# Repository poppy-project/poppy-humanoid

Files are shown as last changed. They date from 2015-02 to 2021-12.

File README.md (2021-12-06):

Poppy Humanoid
===================


Poppy Humanoid is an open-source and 3D printed humanoid robot. Optimized for research and education purposes, its modularity allows for a wide range of applications and experimentations.

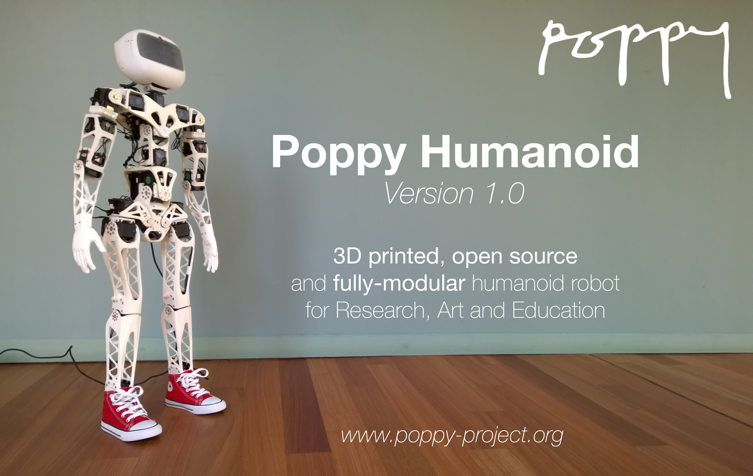
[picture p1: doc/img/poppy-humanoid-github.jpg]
Trunk Assembled


### Open Source

All the technological development work made in the Poppy project is freely available under open source licenses. Only the name usage *"Poppy"* is restricted and protected as an international trademark, please contact us if you want to use it or have more information.

| License | Hardware | Software |
| --- | :---: | :---: |
| Title  | [Creatives Commons BY-SA](http://creativecommons.org/licenses/by-sa/4.0/)  |[GPL v3](http://www.gnu.org/licenses/gpl.html)  |
| Logo  |   |GPL V3 (http://www.gnu.org/licenses/gpl.html)  |

**Please keep references to the [Poppy project (www.poppy-project.org)](https://www.poppy-project.org/) and [authors](doc/authors.md) when you use or fork this work.**

### Looking for the Solidworks files ?

We are using a GitHub feature called GIT LFS. It is great for versionning solidworks files but it stills lack basic features. If you download directly solidworks files from this web page, you will get an empty file...

You have two option:

1. Download the last official Solidworks version in the [release](https://github.com/poppy-project/poppy-humanoid/releases). You will also find STL, STEP and parasolid files.
- Clone locally this repository following [this guide](doc/en/cloning.md). This solution is only for people desiring to contribute or develop news hardware features for Poppy.

## Build your own Poppy Humanoid

Building a complete Poppy Humanoid costs $8000-9000 with about 60% for buying the 25 Robotis Dynamixel actuators required. The full BOM is available here >> [Bill Of Material](https://docs.poppy-project.org/en/assembly-guides/poppy-humanoid/bom.html).

**The STL files are available in [the releases](https://github.com/poppy-project/poppy-humanoid/releases) of this repository.**

Then the process to assemble a complete Poppy Humanoid takes about 7hrs for  handyman people.

**For more informations, refer to the [assembly instructions](https://docs.poppy-project.org/en/assembly-guides/poppy-humanoid/)**.

### Install poppy-humanoid
#### Install a Poppy board
Poppy Humanoid is made to work with a Raspberry Pi 3 or 4. We provide our own [system image](https://github.com/poppy-project/poppy-humanoid/releases) that can be directly copied to the SD-card or MMC. You can refer to the [documentation](http://docs.poppy-project.org/en/installation/burn-an-image-file.html) for more details. Note that if you buy it as a kit from one of the reseller you will also get a pre-installed SD-card.

### Install the software tools locally

You way also connect Poppy Huanoid's motors directly on your own computer with a USB2Dynamixel or USB2AX adapter instead of using the embedded Raspberry Pi 3/4 board. Just install software with pip: `pip install poppy-humanoid`.

**For more informations, refer to the [poppy documentation](http://docs.poppy-project.org/en/installation/index.html)**.

## Support
You need support ?
The [Poppy forum](https://forum.poppy-project.org) is the best (and single) place to ask for help.

You can in particular check for the [Poppy Humanoid category](https://forum.poppy-project.org/c/poppy-creatures/humanoid).

## Contribution

If you are interrested by contribuing to the Poppy project, you can **take a look at [open issues](https://github.com/poppy-project/poppy-humanoid/issues) and [call for contributions](https://forum.poppy-project.org/tags/call-for-contributions)**.

Morevover, the Poppy project involves a very large scope of disciplines:
 - Engineering fields such as computer science, mechanics, electronics, machine learning...
 - Humanities such as cognitive science, psychology...
 - Life science such as biology, biomechanics,...
 - Community management, scientific mediation, communication...
 - Design such as web design, object design, UX,...
 - Art with the need of animator to create [the illusion of life](http://en.wikipedia.org/wiki/Disney_Animation:_The_Illusion_of_Life) and emotions.

So there are many ways to contribute to this project and you are very welcome to do it.

Maybe the first step is to become a member of the community on the [poppy forum](https://forum.poppy-project.org).  The forum is the very central place to exchange with users and contributors. You can freely come and talk about your project or ideas with your prefered language.

For github ninja, you can of course fork this repository and open pull requests to propose your changes, or create issues to notify a problem.

## License

All the technological development work made in the Poppy project is freely available under open source licenses. Only the name usage *"Poppy"* is restricted and protected as an international trademark, please contact us if you want to use it or have more information.

| License | Hardware | Software |
| --- | :---: | :---: |
| Title  | [Creatives Commons BY-SA](http://creativecommons.org/licenses/by-sa/4.0/)  |[GPL v3](http://www.gnu.org/licenses/gpl.html)  |
| Logo  |   |GPL V3 (http://www.gnu.org/licenses/gpl.html)  |

**Please keep references to the [Poppy project (www.poppy-project.org)](https://www.poppy-project.org/) and [authors](doc/authors.md) when you use or fork this work.**

## The Poppy project history

The Poppy project is born in 2012 in the [Flowers laboratory](https://flowers.inria.fr/) at [Inria Bordeaux Sud-Ouest](http://www.inria.fr/en/centre/bordeaux).
It was initiated during [Matthieu Lapeyre](https://github.com/matthieu-lapeyre)'s PhD Thesis surpervised by [Pierre Yves Oudeyer](http://www.pyoudeyer.com/). At the beginning, the development team was composed by [Matthieu Lapeyre](https://github.com/matthieu-lapeyre) (mechanics & design), [Pierre Rouanet](https://github.com/pierre-rouanet) (software) and [Jonathan Grizou](http://jgrizou.com/) (electronics).

This project is initially a fundamental research project financed by [ERC Grant Explorer](http://erc.europa.eu/) to explore the role of embodiement and morphology properties on cognition and especially on the learning of sensori-motor tasks. It is now hosted by the [Poppy Station non-profit](https://www.poppy-station.org/en).

### More on the project

- [Website](https://www.poppy-project.org)
- [Forum](https://forum.poppy-project.org)
- [Twitter](https://twitter.com/poppy_project)
- [Facebook](https://www.facebook.com/poppycommunity/)
- [Flickr](https://www.flickr.com/photos/poppy-project)
- [YouTube](https://www.youtube.com/channel/UC3iVGSr-vMgnFlIfPBH2p7Q)
- [Vimeo](https://vimeo.com/poppyproject/videos)
- [Thingiverse](http://www.thingiverse.com/poppy_project/)

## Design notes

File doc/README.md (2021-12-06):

# Poppy Humanoid

The documentation has moved, please consult the new [assembly guide for Poppy Humanoid](https://docs.poppy-project.org/en/assembly-guides/poppy-humanoid/).

You can still consult the old version: [read the obsolete documentation](https://github.com/poppy-project/poppy-humanoid/tree/6a1ea175f86e1b5a3063007e0c84b435cf22d111#open-source).

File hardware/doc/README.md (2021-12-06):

# Poppy Humanoid BOM

The latest version of the BOM has moved here: [Poppy Humanoid BOM from the assembly guide](https://docs.poppy-project.org/en/assembly-guides/poppy-humanoid/bom.html).

You can still access an archieved version of the [Former Popppy Humanoid BOM](https://github.com/poppy-project/poppy-humanoid/blob/2b6cd60404a45520d8332b1d7d3db10b0ff6218e/hardware/doc/BOM.md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).

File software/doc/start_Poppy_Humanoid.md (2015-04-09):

## Note

Le robot n'est pas prêt pour les démonstrations, il n'y a pas vraiment de sécurité qui va l'empecher de s'auto-detruire en cas de mauvaise manipulation...

## Démarrage

- Brancher le routeur WIFI
- Brancher le robot (12V).

## Connexion

- Se connecter au wifi du routeur
- Normalement, si tout va bien, on doit pouvoir ping le robot:
`ping robot-name.local`
- Si ça ping:
  - se connecter en SSH:
  - `ssh poppy@robot-name.local`
  - `password: odroid`

- Si ça ping pas ...
  - brancher un cable ethernet de la tête au routeur
  - retenter le ping et se connecter en SSH
  - checker ifconfig pour voir si wlan a une IP
    - si non: `sudo reboot`
    - si oui: debrancher l'ethernet et retenter sa chance.

## Play

Une fois connecté en SSH:

- lancer le racourci pour démarrer un ipython notebook:  `bash notebook-launcher`
- se connecter à la page `poppy-humanoid.local:8888`
- et paf tu as un notebook pour coder Poppy et il y a meme quelques trucs déjà prêts.

## Eteindre:

- se connecter en SSH
- `sudo halt`
- attendre un peu et débrancher le robot

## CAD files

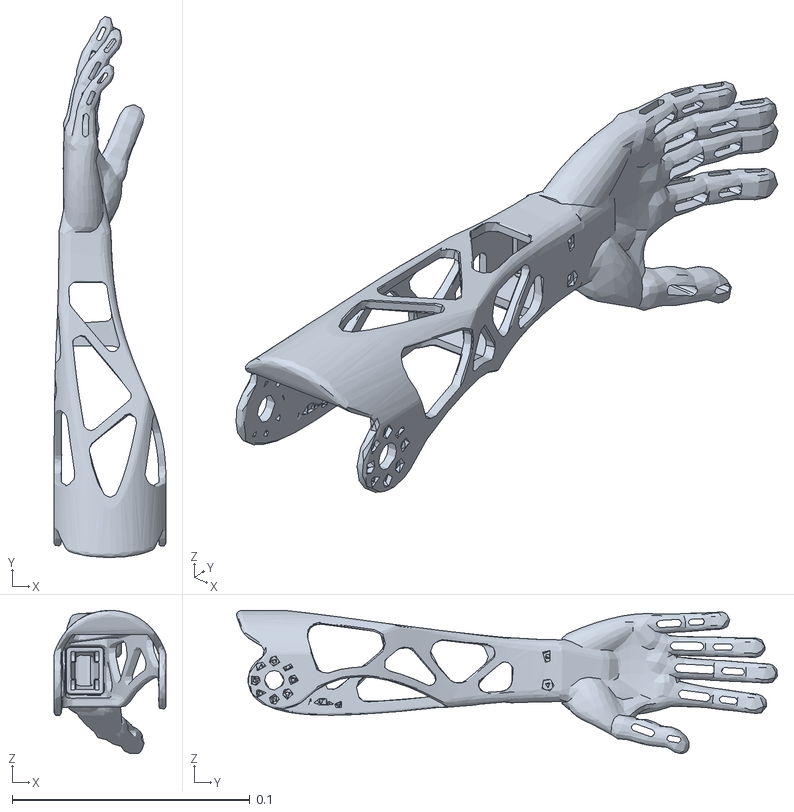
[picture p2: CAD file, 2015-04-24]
hardware/URDF/meshes/r_forearm_visual.STL
0.0471 x 0.228 x 0.0601

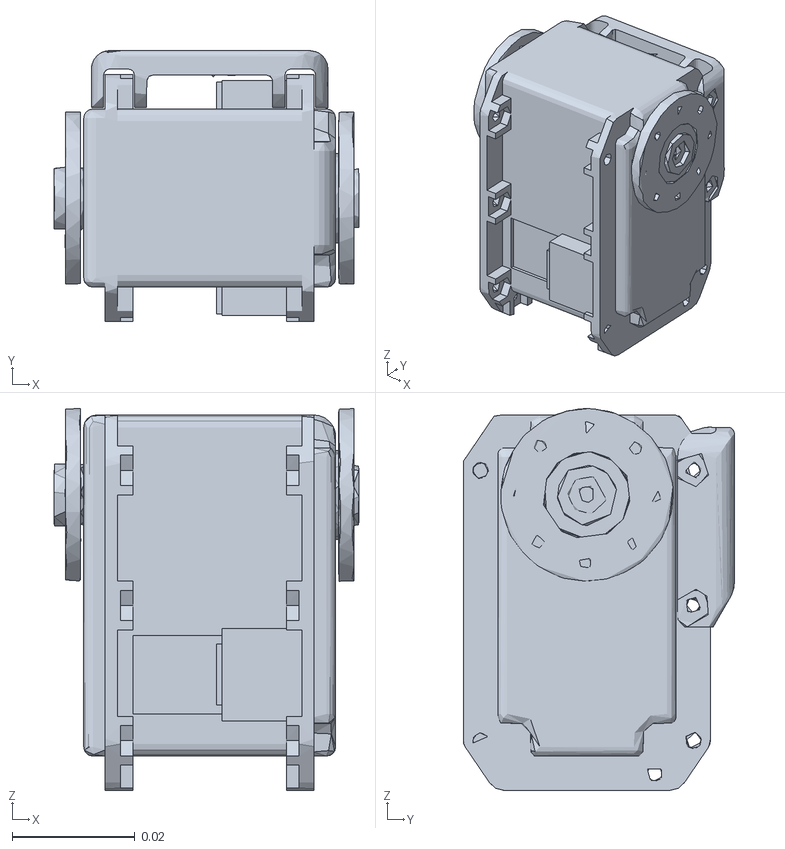
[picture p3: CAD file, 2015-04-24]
hardware/URDF/meshes/r_hip_motor_visual.STL
0.0496 x 0.0441 x 0.0622

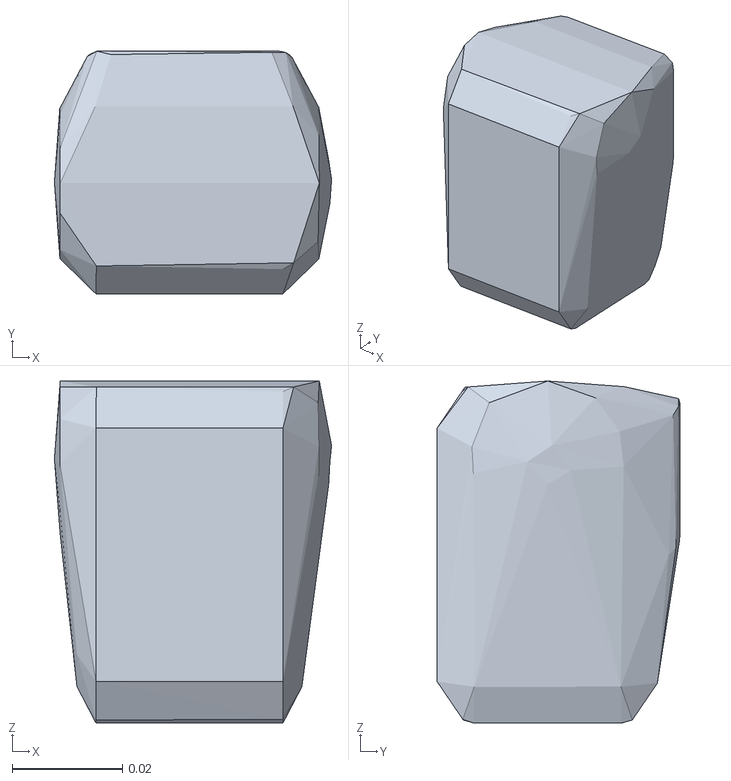
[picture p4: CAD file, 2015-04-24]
hardware/URDF/meshes/l_hip_motor_respondable.stl
0.0504 x 0.0441 x 0.0621

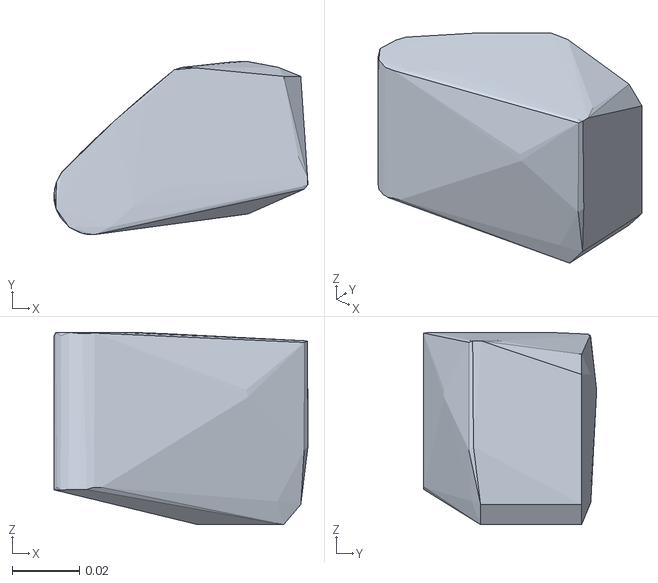
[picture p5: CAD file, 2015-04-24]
hardware/URDF/meshes/l_hip_respondable.stl
0.0754 x 0.0515 x 0.0571

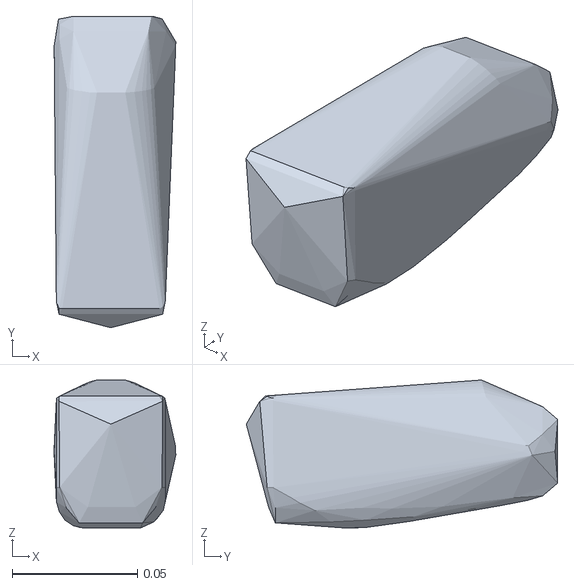
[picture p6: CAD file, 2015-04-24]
hardware/URDF/meshes/l_upper_arm_respondable.STL
0.0486 x 0.124 x 0.0592

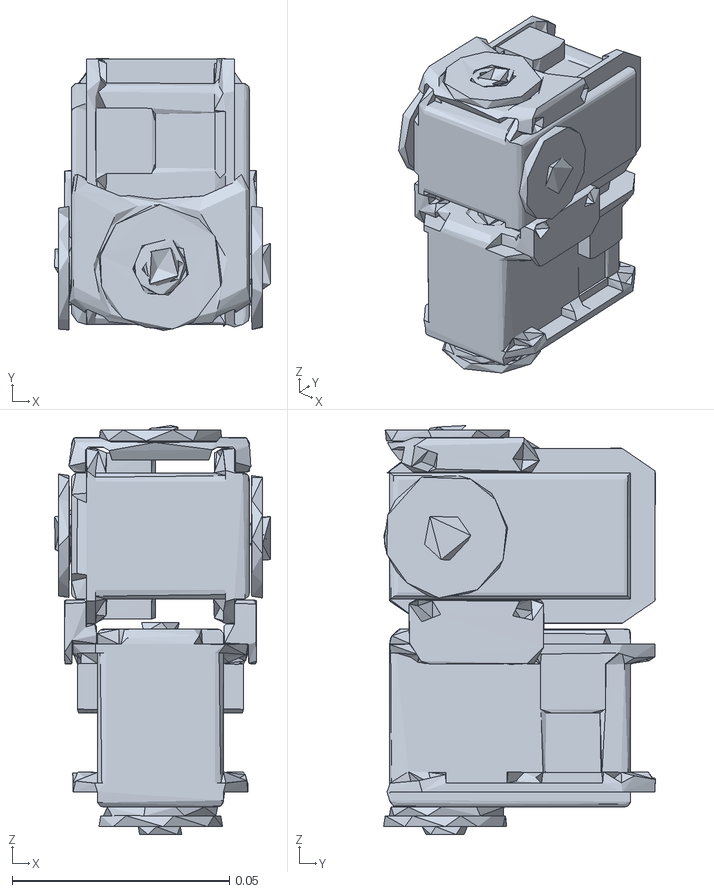
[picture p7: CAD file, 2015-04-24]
hardware/URDF/meshes/abs_motors_visual.STL
0.0497 x 0.0626 x 0.0941

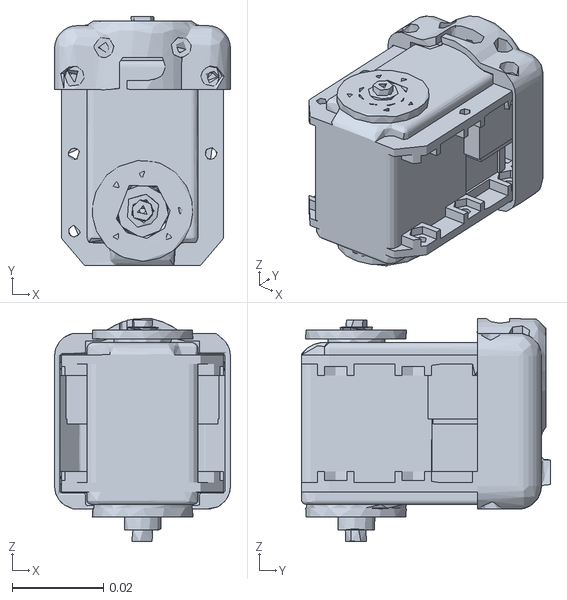
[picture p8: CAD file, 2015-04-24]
hardware/URDF/meshes/l_shoulder_motor_visual.STL
0.0386 x 0.0546 x 0.0489

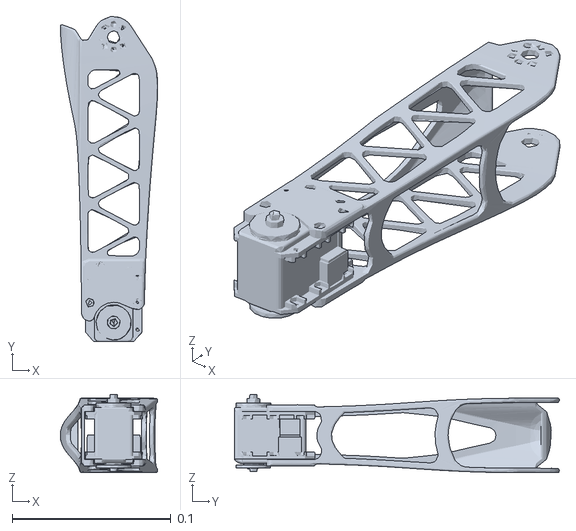
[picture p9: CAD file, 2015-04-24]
hardware/URDF/meshes/r_shin_visual.STL
0.0615 x 0.205 x 0.0495

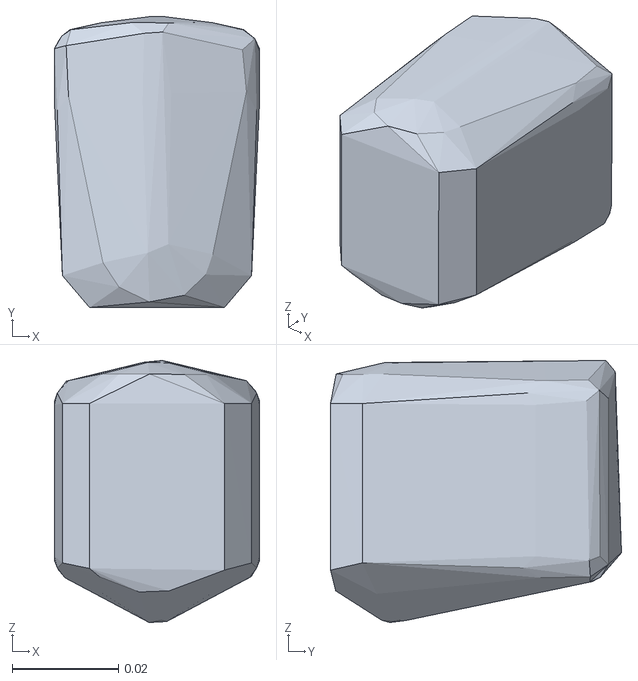
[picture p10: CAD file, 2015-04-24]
hardware/URDF/meshes/r_shoulder_motor_respondable.STL
0.0386 x 0.0548 x 0.0493

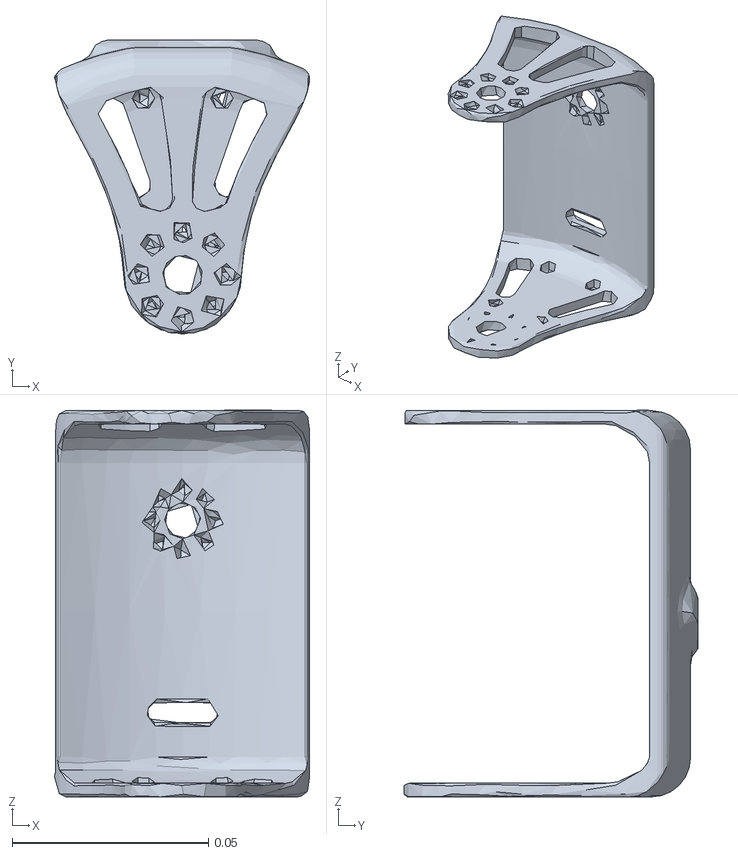
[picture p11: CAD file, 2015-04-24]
hardware/URDF/meshes/abdomen_visual.STL
0.0651 x 0.0749 x 0.0986

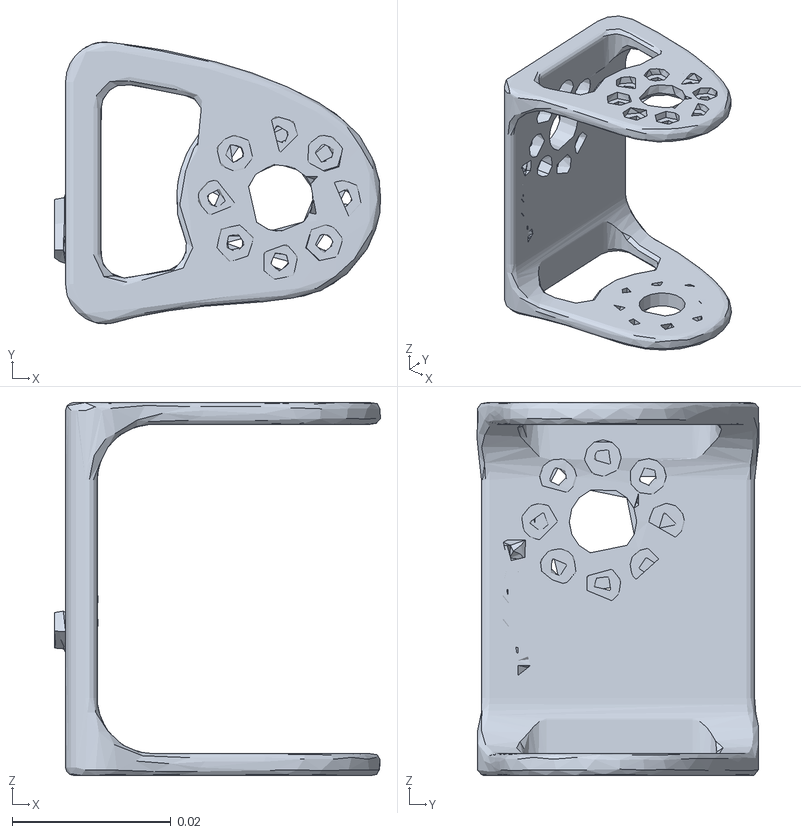
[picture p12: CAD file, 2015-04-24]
hardware/URDF/meshes/l_shoulder_visual.STL
0.0411 x 0.0355 x 0.047

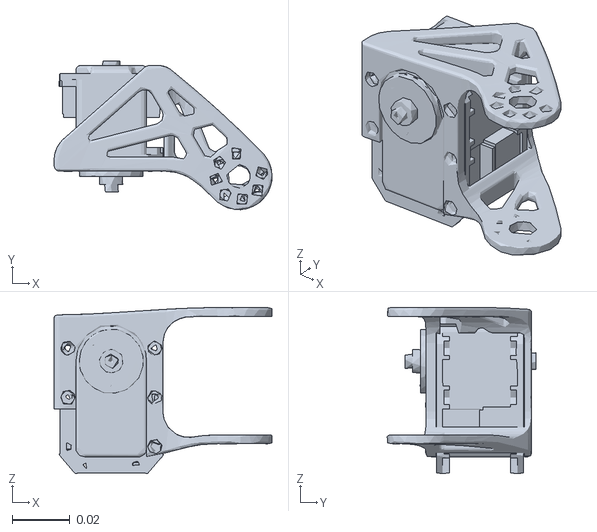
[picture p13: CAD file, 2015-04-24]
hardware/URDF/meshes/r_hip_visual.STL
0.0753 x 0.0514 x 0.0574

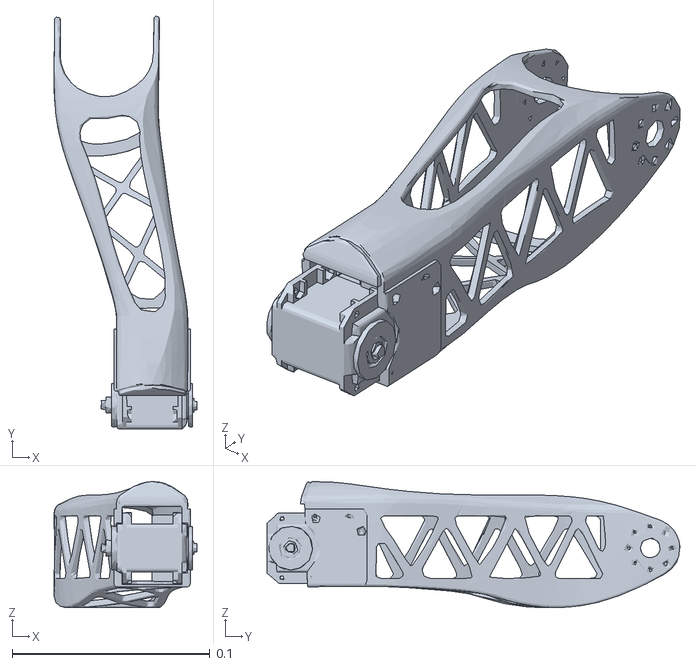
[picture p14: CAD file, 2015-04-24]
hardware/URDF/meshes/r_thigh_visual.STL
0.0724 x 0.209 x 0.0638

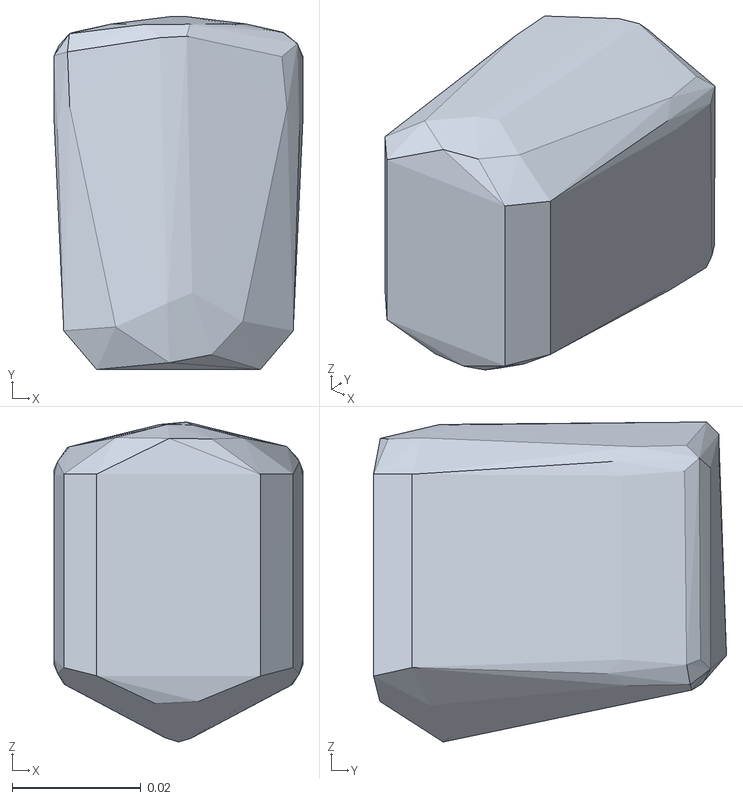
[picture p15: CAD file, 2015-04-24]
hardware/URDF/meshes/l_shoulder_motor_respondable.stl
0.0386 x 0.0548 x 0.0496

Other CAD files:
hardware/URDF/meshes/l_forearm_visual.STL
hardware/URDF/meshes/r_shin_respondable.STL
hardware/URDF/meshes/l_shin_respondable.stl
hardware/URDF/meshes/spine_visual.STL
hardware/URDF/meshes/abdomen_respondable.STL
hardware/URDF/meshes/abs_motors_respondable.stl
hardware/URDF/meshes/bust_motors_respondable.stl
hardware/URDF/meshes/bust_motors_visual.STL
hardware/URDF/meshes/chest_respondable.STL
hardware/URDF/meshes/chest_visual.STL
hardware/URDF/meshes/head_respondable.stl
hardware/URDF/meshes/head_visual.STL
hardware/URDF/meshes/l_foot_respondable.stl
hardware/URDF/meshes/l_foot_visual.STL
hardware/URDF/meshes/l_forearm_respondable.stl
hardware/URDF/meshes/l_hip_motor_visual.STL
hardware/URDF/meshes/l_hip_visual.STL
hardware/URDF/meshes/l_shin_visual.STL
hardware/URDF/meshes/l_shoulder_respondable.stl
hardware/URDF/meshes/l_thigh_respondable.STL
hardware/URDF/meshes/l_thigh_visual.STL
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

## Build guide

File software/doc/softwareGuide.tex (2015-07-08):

\documentclass{article}
\usepackage{graphicx}
\usepackage{hyperref}
\usepackage{color}
\usepackage[utf8]{inputenc}

\begin{document}

\title{Poppy software quickstart guide}
\author{Manon Cortial, Generation Robots}

\maketitle

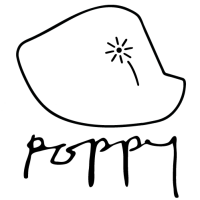
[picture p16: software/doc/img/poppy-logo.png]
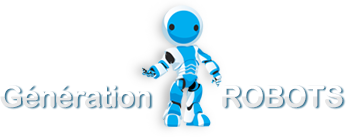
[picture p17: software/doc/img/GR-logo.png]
   \hfill 
  
  \tableofcontents

\section{Introduction}

\subsection{The Poppy Project}

Poppy is an open hardware and open-source project, containing in particular the Poppy Humanoid robot. The Pypot library  was created by the Liris to control the Poppy robots. It is in constant evolution, thanks to the engineers of Liris and to the community, so keep posted.

%The programmation in made essentially in Python, but it is also possible to control the robot with visual programming using Snap!.

%All links to the forum and online documentations are grouped in the section \ref{documentation-links}.

\subsection{How to use this guide?}

This guide gives you an introduction to Poppy programming and helps you to set up your system and find the relevant documentations and tutorials in the Poppy environment.

If you are a \textbf{Poppy user} (beginner, teacher, artist...), you will mostly use the webserver (section \ref{poppy-webservices}) and Snap! (section \ref{programming-with-snap}).

If you are a \textbf{Poppy developer} (student, researcher, application developer...), you want to know about the webserver (section \ref{poppy-webservices}) and the pypot library (section \ref{pypot})

If you \textbf{don't have a Poppy robot}, see section \ref{installing-pypot} to setup your computer, section \ref{v-rep} for the V-REP simulator, then have a look at Snap! (section \ref{programming-with-snap}) or Pypot (section \ref{pypot}).

If you are a \textbf{Poppy contributor}, you want to know about it all! ;-)

\subsection{\textcolor{red}{Safety warning}}

\textbf{The Poppy humanoid robot is built using mainly MX-28 Dynamixel servomotors, which are pretty powerful and may be harmful to your fingers or materials.}

\textbf{So be very careful and put the robot in a free space while testing your programs.}

\subsection{Useful tools}

\subsubsection{Bonjour}

Bonjour is a software made by the Apple company to communicate with a device using its name instead of its IP address.

It is installed by default on Mac and most Linux. Windows users can find an installer here: \url{https://support.apple.com/kb/DL999?locale=fr_FR&viewlocale=fr_FR}

If you don't want to use Bonjour, replace all occurrences of 'poppy.local' by the IP address of the robot in this tutorial.

\subsubsection{SSH}

SSH means Secure SHell. It's a protocol allowing to open a terminal from another device (say, your robot) on your computer.

We will use SSH to have a look at the documents in the robot, change the settings and install new programs. If you are only using the webservices and/or Snap!, you don't need SSH.

SSH is installed by default on Mac and most Linux. The most popular SSH software for Windows is \href{http://www.putty.org/}{Putty}.

\subsubsection{Git and Github}

Git is a versioning software, very useful to secure older versions of your code while working on a new one. It also allows to merge different modifications from different developers on the same project.

Github is a website offering free remote hosting for Git project (if they are public). All sources for Poppy are on \href{https://github.com/poppy-project}{Github}.

Git is not installed by default. For Debian and Fedora based computer, the packet is called git. For Mac, have a look at \url{http://sourceforge.net/projects/git-osx-installer/}. For Windows, find the installer here: \url{http://msysgit.github.io/}.

If you are mainly a user, you will use \textit{git clone} to get new packages and \textit{git pull} to update them.

If you are a developer, quickly create your own account on \url{https://github.com/} and follow the instructions.

%\subsubsection{ipython}

%bla

\section{Poppy Humanoid webservices}
\label{poppy-webservices}

Let assume you have a brand new Poppy Humanoid robot with and embedded Odroid (or Raspberry Pi) board already prepared using the \href{https://github.com/poppy-project/poppy_install}{poppy-install} script.

Connect your Poppy Humanoid robot on your network with an Ethernet cable. Be sure your computer is connected to the same network. Open your web browser and enter:

\begin{verbatim}
http://poppy.local
\end{verbatim}

It opens the Poppy Humanoid web interface, which allows you to:

\begin{itemize}
\item Connect to a local wifi
\item [soon] Put the robot in standing, sitting or compliant position
\item [soon] Record and play moves
\item [soon] Open a ipython console to 
\end{itemize}

\section{Setting up your computer}
\label{installing-pypot}
You may wish to install the Poppy development tool on your computer for several reasons:

\begin{itemize}
\item you have want to use a simulator
\item you want to control a Poppy creature directly plugged on your computer
\item You do lots of development and want an environment friendlier than a webservice or SSH.
\end{itemize}

There are two ways of installing pypot and Poppy-Humanoid on your computer : using pip is easier, but you will get less frequent (but hopefully more stable) software updates. Installing from the sources will get you the latest version of pypot and the possibility to contribute to its development.

\subsection{From pip}
If you're using Ubuntu, Python and pip should be already installed. Otherwise:
\begin{verbatim}
sudo apt-get install python2.7
sudo apt-get install python-pip
\end{verbatim}

Then you simply need to install the Poppy-humanoid package. As pypot is a dependency of Poppy-humanoid, it will be installed too, as well a a few other libraries including numpy and poppy-creature.

\begin{verbatim}
sudo pip install poppy_humanoid
\end{verbatim}

\subsection{From the sources}

The sources of Pyppot are hosted in the \href{https://github.com/poppy-project/pypot}{Poppy project Github}.

To download them, you need to have git installed on your computer. Then, in the folder where you want to put Pypot, you do:

\begin{verbatim}
git clone --recursive https://github.com/poppy-project/pypot.git
\end{verbatim}

Then, you have to install it (so Python can find it):

\begin{verbatim}
cd pypot
python setup.py build
python setup.py install
\end{verbatim}

For the poppy-humanoid sources, follow the same procedure:

\begin{verbatim}
git clone --recursive https://github.com/poppy-project/poppy-humanoid.git
cd ppoppy-humanoid/software
python setup.py build
python setup.py install
\end{verbatim}

\subsection{Test your installation}

In a Python console:

\begin{verbatim}
import pypot, poppy, poppy_humanoid
\end{verbatim}

If one of the imports fails, try to reinstall, to check your PYTHONPATH or check the \href{https://github.com/poppy-project/pypot/issues}{Pypot issues}.

\section{The v-rep Simulator}
\label{v-rep}

v-rep is a 3D robots simulator allowing virtual robots to act in a world with gravity, friction and collisions. The 3D model for Poppy is included in the poppy\_humanoid package.

Be aware that V-rep asks for a fair amount of computation power, so use a decently recent computer.

\subsection{Getting started with v-rep}

First, install the v-rep software corresponding to your computer (\href{http://www.coppeliarobotics.com/downloads.html}{v-rep download page}). This software is free for people of the academical world and there is a free but limited version for other users.

Launch v-rep. On linux:

\begin{verbatim}
cd <path-to-vrep>
./vrep.sh
\end{verbatim}

You should get an empty world with a floor and a tree structure of the elements of the world on the right.

You can explore the world by drag-and-dropping the simulated world and you can start/pause/stop the simulation with the up-right corresponding buttons. As v-rep uses a lots a computing power, it is advised to pause the simulation while your robot don't move.

\subsection{Adding a Poppy}

Open a Python console and type in:

\begin{verbatim}
from poppy_humanoid import PoppyHumanoid
poppy = PoppyHumanoid(simulator='vrep')
\end{verbatim}

The first line imports the PoppyHumanoid object from the poppy\_humanoid library. This object is a Poppy creature with the characteristics of a Poppy robot (see sections \ref{pypot} and \ref{creating-poppy-creature}).

The second line instantiates a PoppyHumanoid creature. It has the \textit{simulator='vrep'} argument to know it should connect to the v-rep server and create a simulated v-rep robot.

In your v-rep world, you should now have a Poppy Humanoid robot.

 \begin{center}
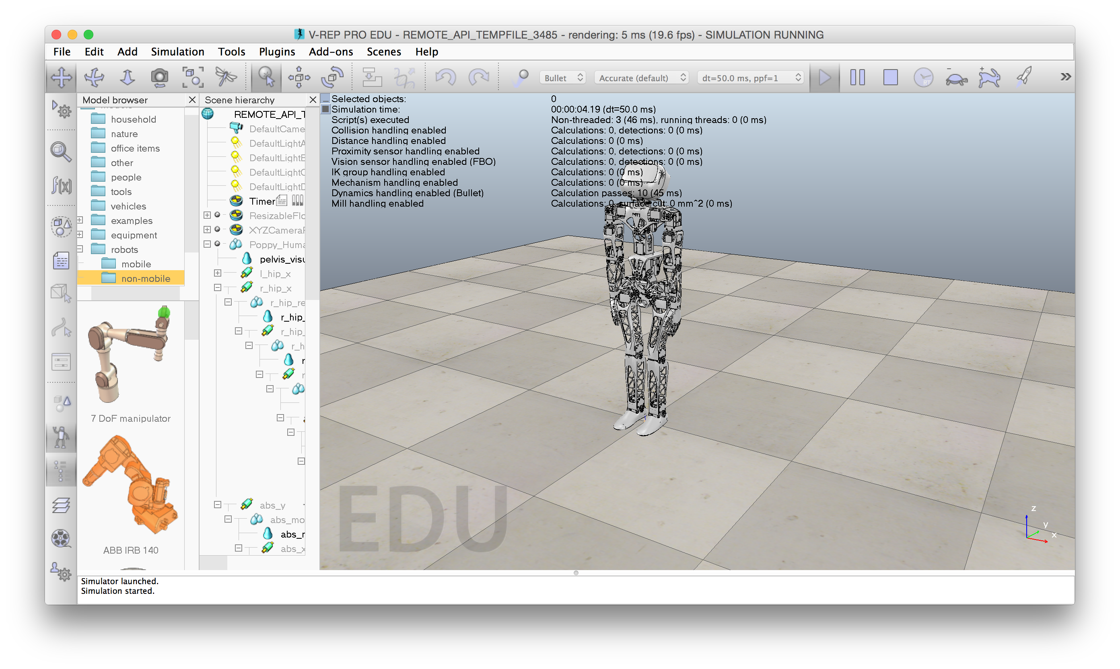
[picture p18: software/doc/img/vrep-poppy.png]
  
 \end{center}
   
Now you can control the simulated Poppy robot as a real robot, as presented in section \ref{pypot}.

\section{Visual programming with snap!}
\label{programming-with-snap}

\subsection{What is snap?}

\href{http://snap.berkeley.edu/}{Snap!} is a "very powerful visual, drag-and-drop programming language. It is an extended reimplementation of Scratch (a project of the Lifelong Kindergarten Group at the MIT Media Lab) that allows you to Build Your Own Blocks". It is an extremely efficient tool to learn how to program for kids or even college students and also a powerful prototyping method for artists.

 \begin{center}
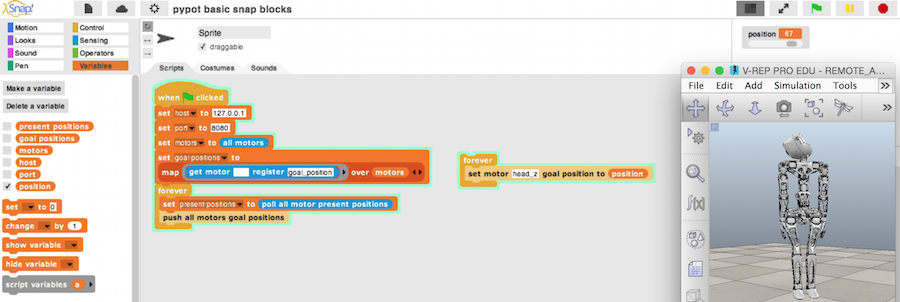
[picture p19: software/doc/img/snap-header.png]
  
 \end{center}

Snap! is open-source and it is entirely written in javascript, you only need a browser connected to the Poppy Creature webserver. No installation is required on your computer!

WARNING! As there is no browser installed by default in Poppy Humanoid's head, you can't use Snap! directly on the robot. You will have to connect the USB2AX to your computer or to use a simulated robot (see V-rep, section \ref{v-rep}).

\subsection{Creating the server}

The first step is to have a server running in the robot or in your computer. The Snap! page will then connect to this server to send orders to the robot.

\subsubsection{On a real Poppy Humanoid robot}

SSH inside the robot and enter the following command:

\begin{verbatim}
poppy-snap poppy-humanoid --no-browser
\end{verbatim}

This will create a PoppyHumanoid object and launch a snap server. It will also return a url (typically \url{http://snap.berkeley.edu/snapsource/snap.html#open:http://<IP>:6969/snap-blocks.xml}).

Enter this address in your web browser.

\subsubsection{On a simulated Poppy Humanoid robot}

For the v-rep simulator, open a Python console and enter:

\begin{verbatim}
from poppy_humanoid import PoppyHumanoid
poppy = PoppyHumanoid(simulator='vrep', use_snap=True)
poppy.snap.run()
\end{verbatim}

Then, open the following url in your web browser: \url{http://snap.berkeley.edu/snapsource/snap.html#open:http://127.0.0.1:6969/snap-blocks.xml}

\subsubsection{Running Snap! locally}

The previous paragraphs make you connect to the Berkeley server and use Snap! online. If you want to avoid this, you can \href{https://github.com/jmoenig/Snap--Build-Your-Own-Blocks}{install} Snap! locally.

Then, in your web browser, open the snap.html file. Import the Poppy specific blocks:

 \begin{center}
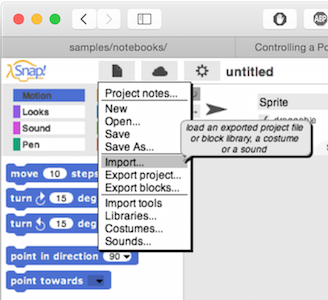
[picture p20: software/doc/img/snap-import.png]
  
 \end{center}

If you have Pypot installed from source, the file pypot-snap-blocks.xml is in the pypot/server folder. Otherwise, you can download only the file:
\begin{verbatim}
wget https://raw.githubusercontent.com/poppy-project/pypot/master/
pypot/server/pypot-snap-blocks.xml
\end{verbatim}

\subsection{Snap! quick start}

The webpage you opened should like like this:

 \begin{center}
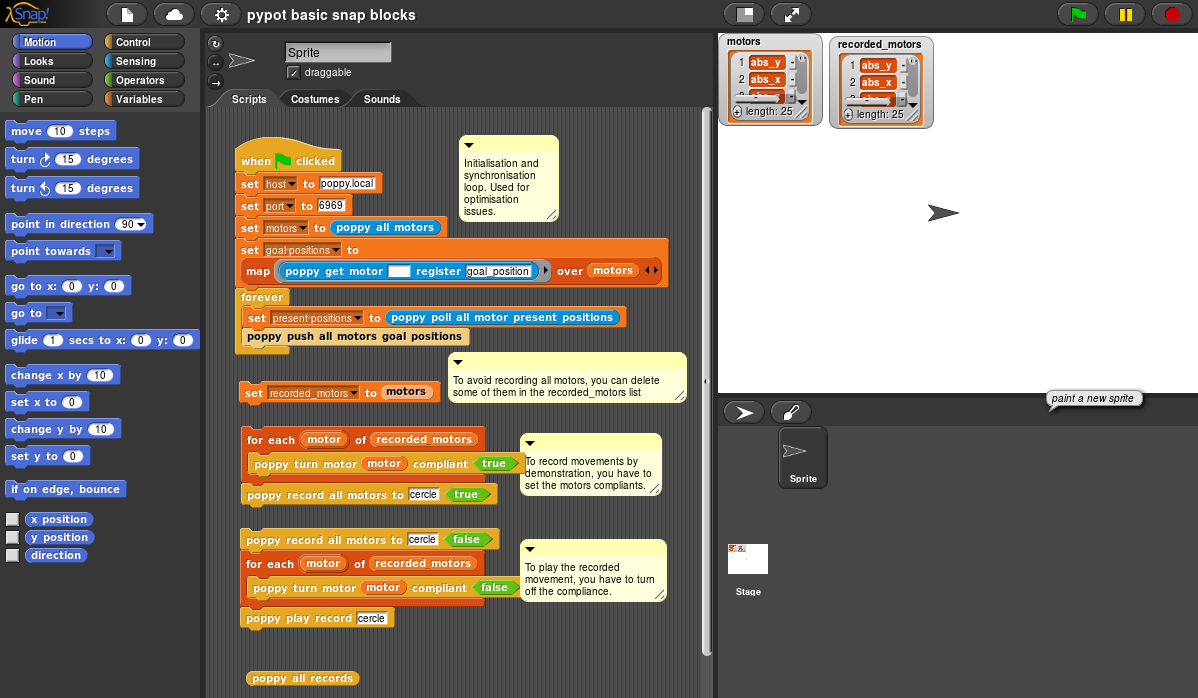
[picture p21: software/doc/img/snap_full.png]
  
 \end{center}

\subsubsection{Synchronization}

The first thing to do is to launch the synchronization loop. Replace the hostname by poppy.local if you use a real Poppy Humanoid robot. Then click on the loop, it should stay highlighted.

 \begin{center}
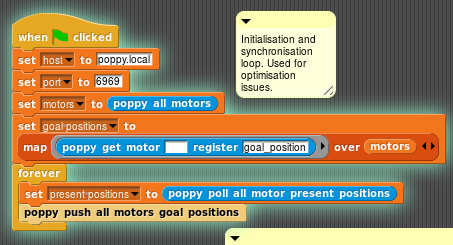
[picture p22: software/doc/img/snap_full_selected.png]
  
 \end{center}

This piece of code first set some variables: host, port, motors and goal-position, the later being created by reading the goal position  ('poppy get motor') of each motor present in the 'motors' array. You can check it by looking at the motors block top right:

 \begin{center}
  
 \end{center}

Then we start a 'forever' loop that read the motors positions ('poppy poll all motors present positions') and store them in a present-positions array. Then it sends to the motors the content of the goal-position array.

This loop is the link between our Snap! code (we will read the present-positions array and modify the goal-positions array) and the real or simulated Poppy robot. You can stop the synchronization loop by clicking on it.

\subsubsection{Poppy blocks}

The default program shows you how to record a movement (called cercle by default):

 \begin{center}
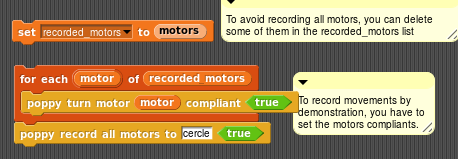
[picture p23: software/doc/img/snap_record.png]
  
 \end{center}
 
 The first line initializes an array containing all motors names. You need to run it only once.
 
 The next block turns all the motors to compliant, so you can move the robot by hand, and starts recording.
 
 To stop recording, click on the next block:

 \begin{center}
  
 \end{center}
 
 This block stops the recording, then removes the compliance so that the robot can move by itself. Then, it starts playing the move you just recorded.
 
 \textbf{Warning}, if you record a move with a name that has already been used, the new movement will be added after the previous one! This may lead to unexpected movements from the robot. Moves are recorded as .record files in the home folder of the Poppy robot.
 
 Other Poppy specific blocks allow you to command each motor separately:
 
  \begin{center}
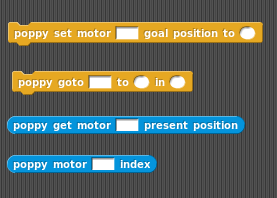
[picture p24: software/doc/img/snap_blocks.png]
  
 \end{center}

For other blocks, see the \href{http://snap.berkeley.edu/SnapManual.pdf}{Snap! reference manual}.

\section{The Pypot library for Poppy}
\label{pypot}

Pypot is a framework developed in the Inria FLOWERS team to make it easy and fast to control custom robots based on Dynamixel motors. This framework provides different level of abstraction corresponding to different types of use, i.e. direct control Robotis motors through a USB2AX, or high-level command of a robot defined by its particular structure.

Pypot has been entirely written in Python to allow for fast development, easy deployment and quick scripting by non-necessary expert developers. The serial communication is handled through the standard library and thus allows for rather high performance (10ms sensorimotor loop). It is crossed-platform and has been tested on Linux, Windows and Mac OS. It is distributed under the GPL V3 open source license.

Pypot is also compatible with the V-REP simulator. This allows you to seamlessly switch from a real robot to its simulated equivalent without having to modify your code.

Documentation can be found \href{http://poppy-project.github.io/pypot/index.html}{here}. %We do only a quick introduction here, find more in the advanced part, section \ref{•}.

\subsection{PoppyHumanoid}

%Use the ipython webservice (when ready) or 
Open a Python console inside the head of your PoppyHumanoid:

\begin{verbatim}
python
\end{verbatim}

The first step to control a Poppy robot with Pypot is to create a Python object corresponding to your robot. We call this object poppy and define it as a PoppyHumanoid:

\begin{verbatim}
from poppy_humanoid import PoppyHumanoid
poppy = PoppyHumanoid()
\end{verbatim}

This PoppyHumanoid object contains a list of motor objects that you can list with:

\begin{verbatim}
print poppy.motors
\end{verbatim}

You get something like:

\begin{verbatim}
[<DxlMotor name=l_elbow_y id=44 pos=-0.0>,
 <DxlMotor name=r_elbow_y id=54 pos=-0.0>,
 <DxlMotor name=r_knee_y id=24 pos=0.2>,
 <DxlMotor name=head_y id=37 pos=-22.7>,
 <DxlMotor name=head_z id=36 pos=0.0>,
 ...
\end{verbatim}

Each motor contain several fields, some static, like name and other directly linked to the corresponding Dynamixel register:

\begin{verbatim}
for m in poppy.motors:
  print "motor ",m.name
  print "  compliance: ",m.compliant,", position: ",m.present_position
\end{verbatim}

You end up with:

\begin{verbatim}
motor  abs_y
  compliance:  True , position:  45.14
motor  abs_x
  compliance:  True , position:  -21.41
motor  abs_z
  compliance:  True , position:  24.22
...
\end{verbatim}

Remember that the angular values are in degrees. When all motors are set to 0, the robot is standing with arms along the body.

You can also control each motor directly:

\begin{verbatim}
print "right ankle angle: ",poppy.r_ankle_y.present_position
\end{verbatim}

\subsection{Simple motor control}

To control a motor, you first need to allow it to use its torque, i.e. to stop being compliant. Let test on the left-right head motor (head\_z).

\begin{verbatim}
poppy.head_z.compliant = False
\end{verbatim}

To prevent the robot from being dangerous, we will limit its maximum torque. You will be able to slightly push the motor with your hand, but it will go back to its goal position. Max torque is an integer value between 0 and 100, a proportion of the physical motor max torque (depends on the motor model).

\begin{verbatim}
poppy.head_z.max_torque=20
\end{verbatim}

Then you have to set the goal position of the register. This operation is instantaneous and the servomotor will try to reach this position using a PID controller. But this is so quick that you will likely not see any delay.

\begin{verbatim}
poppy.head_z.goal_position=20
\end{verbatim}

 The communication with the Dynamixels itself takes some time and is done in parallel. So if you're using Python script, you need to add a bit of delay before the end, as the end of the script destroys you Poppy creature.
 
 \begin{verbatim}
import time
time.sleep(0.1)
\end{verbatim}

\subsection{Timed movements}

If you want a slower movement for your Dynamixel servomotor, you can use the goto\_position function and setting a time for the movement. 

\begin{verbatim}
poppy.head_z.goto_position(-20, 3)
\end{verbatim}

The head should go to angle -20 in 3 seconds.

The wait optional argument allows you to decide if you want the script to return immediately or to wait for the movement completion:

\begin{verbatim}
print "before moving"
poppy.head_z.goto_position(40, 3, wait=True)
print "after first movement completion"
poppy.head_z.goto_position(-40, 3, wait=False)
print "during second movement"
\end{verbatim}

%
%\section{Advanced guide}
%
%
%\subsection{Creating your own Poppy creature}
%\label{creating-poppy-creature}
%
%\subsection{Creating a primitive}
%
%\subsection{Quick look on Dynamixel registers}
%\label{dynamixel-registers}

%use code from others

%anaconda ?

%ipython notebooks ?

\section{Useful links}
\label{documentation-links}

\subsection{Forum and documentations}

\begin{tabular}{lr}

Poppy project website: & \url{https://www.poppy-project.org/} \\ 

Poppy project forum: & \url{https://forum.poppy-project.org/} \\ 
 
Pypot documentation: & \url{http://poppy-project.github.io/pypot/} \\ 

Github: & \url{https://github.com/poppy-project} \\ 

v-rep resources: & \url{http://www.coppeliarobotics.com/resources.html} \\ 
\end{tabular} 

\subsection{Other tutorials}

Poppy in V-REP:

\begin{flushright}
 \href{https://forum.poppy-project.org/t/howto-connect-pypot-to-your-simulated-version-of-a-poppy-humanoid-in-v-rep/332}{https://forum.poppy-project.org/t/howto-connect-pypot-\\to-your-simulated-version-of-a-poppy-humanoid-in-v-rep/332}
 \end{flushright}

Poppy and Snap!:

\begin{flushright}
\href{http://nbviewer.ipython.org/github/poppy-project/pypot/blob/master/samples/notebooks/Controlling%20a%20Poppy%20Creature%20using%20SNAP.ipynb}{http://nbviewer.ipython.org/github/poppy-project/pypot/blob/master/samples/notebooks/Controlling\%20\\a\%20Poppy\%20Creature\%20using\%20SNAP.ipynb}

\end{flushright}

Introduction to Pypot:
\begin{flushright}
\href{http://nbviewer.ipython.org/github/poppy-project/pypot/blob/master/samples/notebooks/QuickStart%20playing%20with%20a%20PoppyErgo.ipynb}{http://nbviewer.ipython.org/github/poppy-project/pypot/blob/master/samples/notebooks/\\QuickStart\%20playing\%20with\%20a\%20PoppyErgo.ipynb} 
\end{flushright}

Record and save moves:
\begin{flushright}
\href{http://nbviewer.ipython.org/github/poppy-project/pypot/blob/master/samples/notebooks/Record%2C%20Save%2C%20and%20Play%20Moves%20on%20a%20Poppy%20Creature.ipynb}{http://nbviewer.ipython.org/github/poppy-project/pypot/blob/master/samples/notebooks/\\Record\%2C\%20Save\%2C\%20and\%20Play\%20Moves\%20\\on\%20a\%20Poppy\%20Creature.ipynb} 
\end{flushright}

\subsection{How to improve this guide?}

You found an imprecision or an error in this guide? We need to correct it!

If you master LaTeX and Github, get the tex file at \href{https://github.com/HumaRobotics/poppy-examples/tree/master/doc}{https://github.com/HumaRobotics/poppy-examples/tree/master/doc} and do a pull request.

Otherwise, go to the forum and point the problem in this topic: \href{https://forum.poppy-project.org/t/quickstart-assembly-and-programming-plus-some-code-examples/1228}{https://forum.poppy-project.org/t/quickstart-assembly-and-programming-plus-some-code-examples/1228}

Thanks in advance!

\end{document}

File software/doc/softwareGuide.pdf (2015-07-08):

# Poppy software quickstart guide

Manon Cortial, Generation Robots

June 9, 2015

## Contents

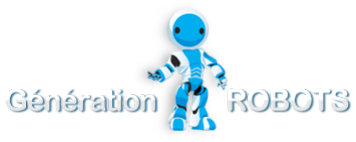
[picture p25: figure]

1 Introduction | 2
2 Poppy Humanoid webservices | 3
3 Setting up your computer | 4
4 The v-rep Simulator | 5
5 Visual programming with snap! | 6

1

6 The Pypot library for Poppy | 11
7 Useful links | 13

## 1 Introduction

### 1.1 The Poppy Project

Poppy is an open hardware and open-source project, containing in particular the Poppy Humanoid robot. The Pypot library was created by the Liris to control the Poppy robots. It is in constant evolution, thanks to the engineers of Liris and to the community, so keep posted.

### 1.2 How to use this guide?

This guide gives you an introduction to Poppy programming and helps you to set up your system and find the relevant documentations and tutorials in the Poppy environment.
If you are a Poppy user (beginner, teacher, artist...), you will mostly use the webserver (section 2) and Snap! (section 5).
If you are a Poppy developer (student, researcher, application developer...), you want to know about the webserver (section 2) and the pypot library (section 6)
If you don’t have a Poppy robot, see section 3 to setup your computer, section 4 for the V-REP simulator, then have a look at Snap! (section 5) or Pypot (section 6).
If you are a Poppy contributor, you want to know about it all! ;-)

### 1.3 Safety warning

The Poppy humanoid robot is built using mainly MX-28 Dynamixel servomotors, which are pretty powerful and may be harmful to your fingers or materials.
So be very careful and put the robot in a free space while testing your programs.

2

### 1.4 Useful tools

### 1.4.1 Bonjour

Bonjour is a software made by the Apple company to communicate with a device using its name instead of its IP address.
It is installed by default on Mac and most Linux. Windows users can find an installer here: https://support.apple.com/kb/DL999?locale=fr_FR&viewlocale=fr_FR (https://support.apple.com/kb/DL999?locale=fr_FR&viewlocale=fr_FR)
If you don’t want to use Bonjour, replace all occurrences of ’poppy.local’ by
the IP address of the robot in this tutorial.

### 1.4.2 SSH

SSH means Secure SHell. It’s a protocol allowing to open a terminal from another device (say, your robot) on your computer.
We will use SSH to have a look at the documents in the robot, change the settings and install new programs. If you are only using the webservices and/or Snap!, you don’t need SSH.
SSH is installed by default on Mac and most Linux. The most popular SSH software for Windows is Putty. (http://www.putty.org/)

### 1.4.3 Git and Github

Git is a versioning software, very useful to secure older versions of your code while working on a new one. It also allows to merge different modifications from different developers on the same project.
Github is a website offering free remote hosting for Git project (if they are public). All sources for Poppy are on Github. (https://github.com/poppy-project)
Git is not installed by default. For Debian and Fedora based computer, the packet is called git. For Mac, have a look at http://sourceforge.net/projects/git-osx-installer/. (http://sourceforge.net/projects/git-osx-installer/) For Windows, find the installer here: http: //msysgit.github.io/.
If you are mainly a user, you will use git clone to get new packages and git pull to update them.
If you are a developer, quickly create your own account on https://github.com/ (https://github.com/) and follow the instructions.

## 2 Poppy Humanoid webservices

Let assume you have a brand new Poppy Humanoid robot with and embedded Odroid (or Raspberry Pi) board already prepared using the poppy-install (https://github.com/poppy-project/poppy_install) script. Connect your Poppy Humanoid robot on your network with an Ethernet cable. Be sure your computer is connected to the same network. Open your web browser and enter:

http://poppy.local

3

It opens the Poppy Humanoid web interface, which allows you to:

- Connect to a local wifi

soon Put the robot in standing, sitting or compliant position

soon Record and play moves

soon Open a ipython console to

## 3 Setting up your computer

You may wish to install the Poppy development tool on your computer for several reasons:

- you have want to use a simulator
- you want to control a Poppy creature directly plugged on your computer
- You do lots of development and want an environment friendlier than a webservice or SSH.

There are two ways of installing pypot and Poppy-Humanoid on your computer : using pip is easier, but you will get less frequent (but hopefully more stable) software updates. Installing from the sources will get you the latest version of pypot and the possibility to contribute to its development.

### 3.1 From pip

If you’re using Ubuntu, Python and pip should be already installed. Otherwise:

sudo apt-get install python2.7
sudo apt-get install python-pip

Then you simply need to install the Poppy-humanoid package. As pypot is a dependency of Poppy-humanoid, it will be installed too, as well a a few other libraries including numpy and poppy-creature.

sudo pip install poppy_humanoid

### 3.2 From the sources

The sources of Pyppot are hosted in the Poppy project Github. (https://github.com/poppy-project/pypot)
To download them, you need to have git installed on your computer. Then, in the folder where you want to put Pypot, you do:

git clone --recursive https://github.com/poppy-project/pypot.git

Then, you have to install it (so Python can find it):

4

cd pypot
python setup.py build
python setup.py install

For the poppy-humanoid sources, follow the same procedure:

git clone --recursive https://github.com/poppy-project/poppy-humanoid.git cd ppoppy-humanoid/software
python setup.py build
python setup.py install

### 3.3 Test your installation

In a Python console:

import pypot, poppy, poppy_humanoid

If one of the imports fails, try to reinstall, to check your PYTHONPATH or check the Pypot issues. (https://github.com/poppy-project/pypot/issues)

## 4 The v-rep Simulator

v-rep is a 3D robots simulator allowing virtual robots to act in a world with gravity, friction and collisions. The 3D model for Poppy is included in the poppy humanoid package.
Be aware that V-rep asks for a fair amount of computation power, so use a decently recent computer.

### 4.1 Getting started with v-rep

First, install the v-rep software corresponding to your computer (v-rep download page). (http://www.coppeliarobotics.com/downloads.html) This software is free for people of the academical world and there is a free but limited version for other users.
Launch v-rep. On linux:

cd <path-to-vrep>
./vrep.sh

You should get an empty world with a floor and a tree structure of the elements of the world on the right.
You can explore the world by drag-and-dropping the simulated world and you can start/pause/stop the simulation with the up-right corresponding buttons. As v-rep uses a lots a computing power, it is advised to pause the simulation while your robot don’t move.

5

### 4.2 Adding a Poppy

Open a Python console and type in:

from poppy_humanoid import PoppyHumanoid
poppy = PoppyHumanoid(simulator=’vrep’)

The first line imports the PoppyHumanoid object from the poppy humanoid library. This object is a Poppy creature with the characteristics of a Poppy robot (see sections 6 and ??).
The second line instantiates a PoppyHumanoid creature. It has the simulator=’vrep’ argument to know it should connect to the v-rep server and create a simulated v-rep robot.
In your v-rep world, you should now have a Poppy Humanoid robot.

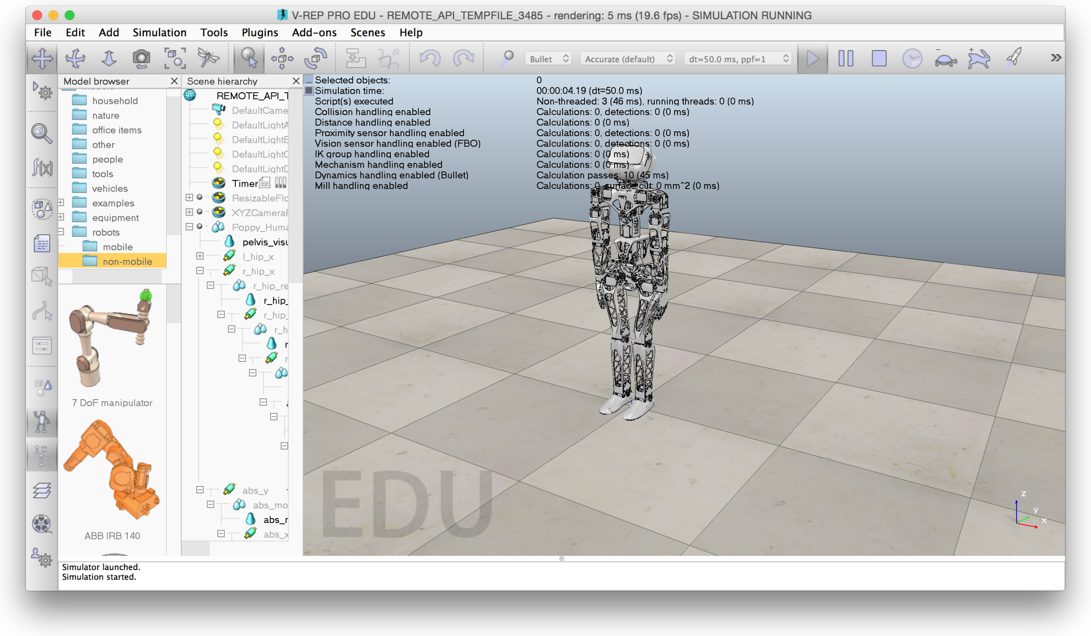
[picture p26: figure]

Now you can control the simulated Poppy robot as a real robot, as presented in section 6.

## 5 Visual programming with snap!

### 5.1 What is snap?

Snap! (http://snap.berkeley.edu/) is a ”very powerful visual, drag-and-drop programming language. It is an extended reimplementation of Scratch (a project of the Lifelong Kindergarten Group at the MIT Media Lab) that allows you to Build Your Own Blocks”. It is an extremely efficient tool to learn how to program for kids or even college students and also a powerful prototyping method for artists.

6

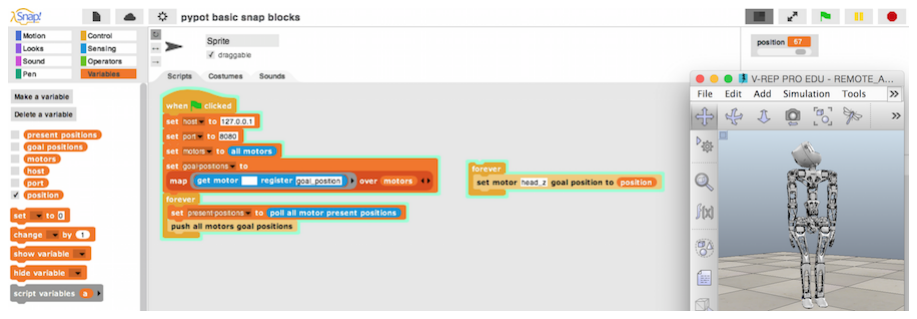
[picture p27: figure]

Snap! is open-source and it is entirely written in javascript, you only need a browser connected to the Poppy Creature webserver. No installation is required on your computer!
WARNING! As there is no browser installed by default in Poppy Humanoid’s head, you can’t use Snap! directly on the robot. You will have to connect the USB2AX to your computer or to use a simulated robot (see V-rep, section 4).

### 5.2 Creating the server

The first step is to have a server running in the robot or in your computer. The Snap! page will then connect to this server to send orders to the robot.

### 5.2.1 On a real Poppy Humanoid robot

SSH inside the robot and enter the following command:

poppy-snap poppy-humanoid --no-browser

This will create a PoppyHumanoid object and launch a snap server. It will also return a url (typically http://snap.berkeley.edu/snapsource/snap.html#open:http://<IP>:6969/snap-blocks.xml). (http://snap.berkeley.edu/snapsource/snap.html#open:http://<IP>:6969/snap-blocks.xml)
Enter this address in your web browser.

### 5.2.2 On a simulated Poppy Humanoid robot

For the v-rep simulator, open a Python console and enter:

from poppy_humanoid import PoppyHumanoid
poppy = PoppyHumanoid(simulator=’vrep’, use_snap=True) poppy.snap.run()

Then, open the following url in your web browser: http://snap.berkeley.edu/snapsource/snap.html#open:http://127.0.0.1:6969/snap-blocks.xml (http://snap.berkeley.edu/snapsource/snap.html#open:http://127.0.0.1:6969/snap-blocks.xml)

7

### 5.2.3 Running Snap! locally

The previous paragraphs make you connect to the Berkeley server and use Snap! online. If you want to avoid this, you can install (https://github.com/jmoenig/Snap--Build-Your-Own-Blocks) Snap! locally.
Then, in your web browser, open the snap.html file. Import the Poppy specific blocks:

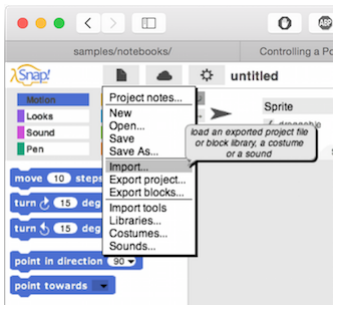
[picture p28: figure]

If you have Pypot installed from source, the file pypot-snap-blocks.xml is in the pypot/server folder. Otherwise, you can download only the file:

wget https://raw.githubusercontent.com/poppy-project/pypot/master/pypot/server/pypot-snap-blocks.xml

### 5.3 Snap! quick start

The webpage you opened should like like this:

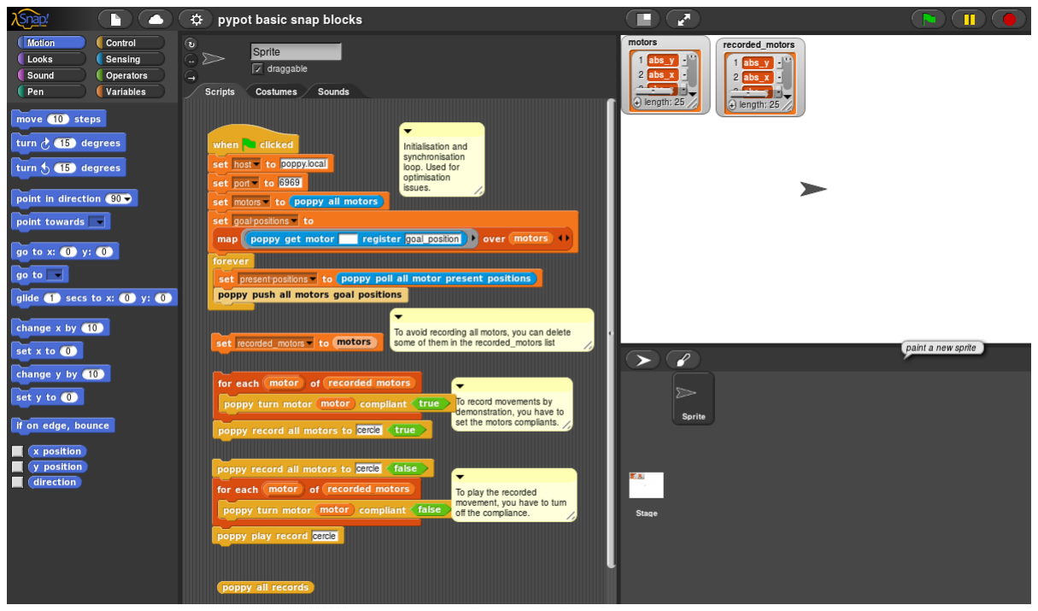
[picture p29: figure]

8

### 5.3.1 Synchronization

The first thing to do is to launch the synchronization loop. Replace the hostname by poppy.local if you use a real Poppy Humanoid robot. Then click on the loop, it should stay highlighted.

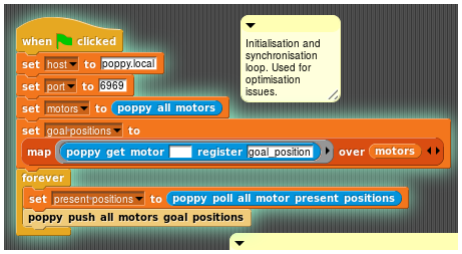
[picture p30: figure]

This piece of code first set some variables: host, port, motors and goal-position, the later being created by reading the goal position (’poppy get motor’) of each motor present in the ’motors’ array. You can check it by looking at the motors block top right:

Then we start a ’forever’ loop that read the motors positions (’poppy poll all motors present positions’) and store them in a present-positions array. Then it sends to the motors the content of the goal-position array.
This loop is the link between our Snap! code (we will read the present-positions array and modify the goal-positions array) and the real or simulated Poppy robot. You can stop the synchronization loop by clicking on it.

### 5.3.2 Poppy blocks

The default program shows you how to record a movement (called cercle by default):

9

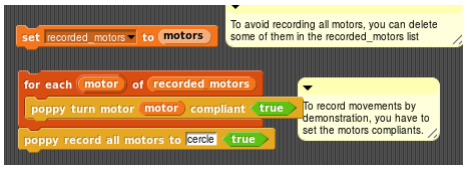
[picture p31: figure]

The first line initializes an array containing all motors names. You need to run it only once.
The next block turns all the motors to compliant, so you can move the robot by hand, and starts recording.
To stop recording, click on the next block:

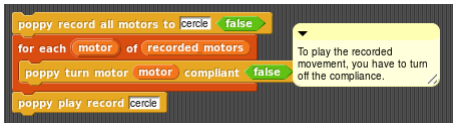
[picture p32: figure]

This block stops the recording, then removes the compliance so that the robot can move by itself. Then, it starts playing the move you just recorded. Warning, if you record a move with a name that has already been used, the new movement will be added after the previous one! This may lead to unexpected movements from the robot. Moves are recorded as .record files in the home folder of the Poppy robot.
Other Poppy specific blocks allow you to command each motor separately:

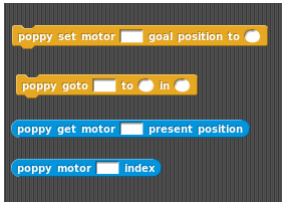
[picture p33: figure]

For other blocks, see the Snap! reference manual. (http://snap.berkeley.edu/SnapManual.pdf)

10

## 6 The Pypot library for Poppy

Pypot is a framework developed in the Inria FLOWERS team to make it easy and fast to control custom robots based on Dynamixel motors. This framework provides different level of abstraction corresponding to different types of use, i.e. direct control Robotis motors through a USB2AX, or high-level command of a robot defined by its particular structure.
Pypot has been entirely written in Python to allow for fast development, easy deployment and quick scripting by non-necessary expert developers. The serial communication is handled through the standard library and thus allows for rather high performance (10ms sensorimotor loop). It is crossed-platform and has been tested on Linux, Windows and Mac OS. It is distributed under the GPL V3 open source license.
Pypot is also compatible with the V-REP simulator. This allows you to seamlessly switch from a real robot to its simulated equivalent without having to modify your code.
Documentation can be found here. (http://poppy-project.github.io/pypot/index.html)

### 6.1 PoppyHumanoid

Open a Python console inside the head of your PoppyHumanoid:

python

The first step to control a Poppy robot with Pypot is to create a Python object corresponding to your robot. We call this object poppy and define it as a PoppyHumanoid:

from poppy_humanoid import PoppyHumanoid
poppy = PoppyHumanoid()

This PoppyHumanoid object contains a list of motor objects that you can list with:

print poppy.motors

You get something like:

[<DxlMotor name=l_elbow_y id=44 pos=-0.0>, <DxlMotor name=r_elbow_y id=54 pos=-0.0>, <DxlMotor name=r_knee_y id=24 pos=0.2>, <DxlMotor name=head_y id=37 pos=-22.7>, <DxlMotor name=head_z id=36 pos=0.0>,

Each motor contain several fields, some static, like name and other directly linked to the corresponding Dynamixel register:

11

for m in poppy.motors:
print "motor ",m.name
print " compliance: ",m.compliant,", position: ",m.present_position

You end up with:

motor | abs_y
compliance: | True , position: | 45.14
motor | abs_x
compliance: | True , position: | -21.41
motor | abs_z
compliance: | True , position: | 24.22

Remember that the angular values are in degrees. When all motors are set to 0, the robot is standing with arms along the body.
You can also control each motor directly:

print "right ankle angle: ",poppy.r_ankle_y.present_position

### 6.2 Simple motor control

To control a motor, you first need to allow it to use its torque, i.e. to stop being compliant. Let test on the left-right head motor (head z).

poppy.head_z.compliant = False

To prevent the robot from being dangerous, we will limit its maximum torque. You will be able to slightly push the motor with your hand, but it will go back to its goal position. Max torque is an integer value between 0 and 100, a proportion of the physical motor max torque (depends on the motor model).

poppy.head_z.max_torque=20

Then you have to set the goal position of the register. This operation is instantaneous and the servomotor will try to reach this position using a PID controller. But this is so quick that you will likely not see any delay.

poppy.head_z.goal_position=20

The communication with the Dynamixels itself takes some time and is done in parallel. So if you’re using Python script, you need to add a bit of delay before the end, as the end of the script destroys you Poppy creature.

import time
time.sleep(0.1)

12

### 6.3 Timed movements

If you want a slower movement for your Dynamixel servomotor, you can use the goto position function and setting a time for the movement.

poppy.head_z.goto_position(-20, 3)

The head should go to angle -20 in 3 seconds.
The wait optional argument allows you to decide if you want the script to return immediately or to wait for the movement completion:

print "before moving"
poppy.head_z.goto_position(40, 3, wait=True)
print "after first movement completion" poppy.head_z.goto_position(-40, 3, wait=False) print "during second movement"

## 7 Useful links

### 7.1 Forum and documentations

Poppy project website: | https://www.poppy-project.org/
Poppy project forum: | https://forum.poppy-project.org/
Pypot documentation: | http://poppy-project.github.io/pypot/
Github: | https://github.com/poppy-project
v-rep resources: | http://www.coppeliarobotics.com/resources.html

### 7.2 Other tutorials

Poppy in V-REP:

https://forum.poppy-project.org/t/howto-connect-pypotto-your-simulated-version-of-a-poppy-humanoid-in-v-rep/332 (https://forum.poppy-project.org/t/howto-connect-pypot-to-your-simulated-version-of-a-poppy-humanoid-in-v-rep/332)

Poppy and Snap!:

| http://nbviewer.ipython.org/github/poppy-
project/pypot/blob/master/samples/notebooks/Controlling%20
| a%20Poppy%20Creature%20using%20SNAP.ipynb (http://nbviewer.ipython.org/github/poppy-project/pypot/blob/master/samples/notebooks/Controlling%20a%20Poppy%20Creature%20using%20SNAP.ipynb)

Introduction to Pypot:

| http://nbviewer.ipython.org/github/poppy-
| project/pypot/blob/master/samples/notebooks/
QuickStart%20playing%20with%20a%20PoppyErgo.ipynb (http://nbviewer.ipython.org/github/poppy-project/pypot/blob/master/samples/notebooks/QuickStart%20playing%20with%20a%20PoppyErgo.ipynb)

Record and save moves:

| http://nbviewer.ipython.org/github/poppy-
| project/pypot/blob/master/samples/notebooks/
Record%2C%20Save%2C%20and%20Play%20Moves%20
| on%20a%20Poppy%20Creature.ipynb (http://nbviewer.ipython.org/github/poppy-project/pypot/blob/master/samples/notebooks/Record%2C%20Save%2C%20and%20Play%20Moves%20on%20a%20Poppy%20Creature.ipynb)

13

### 7.3 How to improve this guide?

You found an imprecision or an error in this guide? We need to correct it!
If you master LaTeX and Github, get the tex file at https://github.com/HumaRobotics/poppyexamples/tree/master/doc (https://github.com/HumaRobotics/poppy-examples/tree/master/doc) and do a pull request.
Otherwise, go to the forum and point the problem in this topic: https://forum.poppy-project.org/t/quickstart-assembly-and-programming-plus-some-code-examples/1228 (https://forum.poppy-project.org/t/quickstart-assembly-and-programming-plus-some-code-examples/1228)
Thanks in advance!

14

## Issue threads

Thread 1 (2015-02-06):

Increase tolerances for the leg/motor assemblies

matthieu-lapeyre, 2015-02-06:

jgrizou, 2015-02-06:
Tolerance to change:
- tolerance on the side of motors.
- tolerance on the depth of the ollo head.
- tolerance on the diameter of the ollo holes.

matthieu-lapeyre, 2015-02-24:
wrong repository ==> moved to https://github.com/poppy-project/Poppy-lightweight-biped-legs/issues/2

Closed 2015-02-24.

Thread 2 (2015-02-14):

STL files not scaled for 3d printing

rjduran, 2015-02-14:
The mesh files are not scaled to the actual physical size when printed. I'm new to the project so I have not yet configured everything. Do the files get scaled somewhere in software? For example, the l_foot.stl file has the dimensions L = 0.05mm, W = 0.04mm, H = 0.15mm

matthieu-lapeyre, 2015-02-14:
Yep it's my fault, I wrongly exported file into "meter" instead of "millimeter"...

I explained it here:https://forum.poppy-project.org/t/release-of-poppy-1-0-price-and-date/928/

I will try to re-export them ASAP.

rjduran, 2015-02-14:
Got it. Thanks!

matthieu-lapeyre, 2015-02-14:
I keep it open until I solve it.

Thanks for raising it as an issue.

matthieu-lapeyre, 2015-02-18:
New export available here: https://github.com/poppy-project/poppy-humanoid/releases/download/1.0-pre-release/STL_3D_printed_parts.zip

I also created a tutorial and a python script to simplify the STL export of 3D printed parts from Solidworks. See here: https://github.com/poppy-project/poppy-humanoid/tree/master/hardware/doc/Poppy_Humanoid_assembly_instructions.md

Closed 2015-02-18.

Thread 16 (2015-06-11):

Update motor_naming_convention

show0k, 2015-06-11:
It will be usefull to update [motor_naming_convention.pdf](https://forum.poppy-project.org/t/assembly-instructions-motor-naming-convention-and-configuration/87) file with the new poppy hardware setup. A png file (with alpha layer) may be more appropriate than a pdf (which use jpeg compression).

matthieu-lapeyre, 2015-10-02:
It is on the way
https://www.flickr.com/photos/poppy-project/21696451449/in/dateposted-public/

show0k, 2015-11-05:
Any advance on that ?

matthieu-lapeyre, 2015-11-05:
https://forum.poppy-project.org/t/versionning-et-documentation/1660/33?u=matthieu

show0k, 2015-11-05:
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

matthieu-lapeyre, 2015-11-24:
Tu n'en avais pas fait un pour l'Humanoid ? Je ne trouve plus la photo

[--- Commented from Asana.com
#commenter Théo Segonds
---[aa]

Closed 2022-10-15.

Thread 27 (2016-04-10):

Release download is veeerryyy slow

matthieu-lapeyre, 2016-04-10:
It takes ages to download the iso from the release.
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

I do not have fiber connection yet 150 Kb/s is far from the max I can reach...

Maybe we should have a mirror with better performance ?

pierre-rouanet, 2016-04-11:
On my side, no problem. I download at the maximum of my bandwidth capacities.

Did you check https://status.github.com maybe they were just having some server issues?

matthieu-lapeyre, 2016-04-11:
indeed, today it downloads at a normal speed.

show0k, 2016-04-11:
Btw, releases are hosted on Amazon S3 ; I checked issues report and see nothing.

Closed 2016-04-11.

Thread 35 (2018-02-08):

Error while connecting the Poppy Humanoid robot to the PC

shashankboosi, 2018-02-08:
Hello there,

I tried many ways and I finally am able to ping the robot in my PC. I used http://poppy.local and I was able to open the web interface. I am trying to run the robot on Windows platform on my PC but the odroid board in the robot has a Ubuntu Linux platform. I tried to link the humanoid with my PC using the ethernet cable via a switch and I was able to ping the IP address of the robot from the PC. only when I type http://10.118.18.89/ I get the following web interface which seems to be working

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

but if I type http://poppy.local I got an error message saying the following

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

But I ignored the poppy.local link and I have approached the web interface using the IP address. If I go to python terminal, it says connection failed. And I got these errors in the log file of web interface:

Logs:

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

Then I decided to go to the ipython notebook not through the web interface of the robot but through the anaconda navigator and I wrote the following code to see what happens

```
from pypot.creatures import PoppyHumanoid
poppy = PoppyHumanoid()
```
Then I got the following errors in the log:

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

So the problem is that, I am not able to operate the web interface properly and I am getting all sorts of errors. Even the odroid board blinks with a blue light, does that mean something? Because blue light in Rasberry pi means the core is crashed.

> Even sometimes I get this error where it says multiple access on ports
> It also says, the data is received by the robot but cannot be sent back to the PC.

I hope I have explained my doubt. If not please let me know
Any insights into this will be appreciated.

Thanks in advance for the help.

ymollard, 2022-10-15:
Closing old issues (please use the forum to ask for help)

Closed 2022-10-15.

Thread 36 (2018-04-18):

Find suitable replacement for actuators

Pepetruen0, 2018-04-18:
At $9k, this project is not approachable for hobbyists. I just found this project and was thinking of building one until I saw the BOM cost. Will check back in a couple of years.

SX-GitHub, 2020-11-23:
This robot is not designed to use toy servos. Robotis servos dominant this sector and all colleges and labs are using them. I found Kondo servos are superior in specs and cost, but they are not drop-in replacements and difficult to find outside of Japan.

vkarpuram, 2021-03-22:
What about the Lynxmotion Smart Servo: https://www.robotshop.com/en/lynxmotion-smart-servo-lss-high-torque-ht1.html

bevinhex, 2021-05-17:
should be able to replace with cheaper server with equal torque, I suppose you could use small PIC/AVR micro controllers to output pwm to drive one serve then use i2c to daisy-chain them, thus things like current sensing can be done out of servo, I'm not too sure yet, but since nobody needs all those super-duper sensing/configurations provided, depending on your need, should be fine.
cheap 60kg servo is 45$, 20kg servo 17$, only problem is you also need to touch CAD to adapt things to it.
most important question is what sensor or functionality do we need to do what, look at this guy https://ai2001.ifdef.jp/, the servos he is using seems pretty ordinary, yet it can drag heavy objects and adapt to it

gl0p, 2022-01-11:
Ive always been interested in making my own little robot and this year i am attempting to design my own, im using the 50$ 60 kg servos, buying two at a time as i go. Just starting off using raspi picos to get it going. Id like to make something cheap enough for people to take interest in. Kind of a bare bones project i guess, something scaleable for different size actuators... we will see.

ymollard, 2022-10-15:
Closing old issues. Please use the forum for anything that is not a bug.
The forum has several threads about using cheaper motors, e.g. https://poppy.discourse.group/t/is-it-possible-to-replace-robotis-actuators-by-cheaper-ones/128

Closed 2022-10-15.

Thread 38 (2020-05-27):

Difference between the URDF and VREP models

mathieu-celerier, 2020-05-27:
I've been working on poppy at schools for few months now, working on compliant control.

I'm only working in simulation on V-REP for the moment, I use the URDF to rebuild the complete model of the robot in my program, and I noticed a difference on the r_soulder_x.

While standing up, arms down in V-REP, the robot plot from URDF have the right arm straight up.

Is it an issue or an intended behaviour ?

Mat
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

ymollard, 2020-05-27:
This is unintended I guess, now let's try to find the issue :)

I think that link should be rotated to match the left side:
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

I would say that yaw = -1.5707963267949 [there](https://github.com/poppy-project/poppy-humanoid/blob/master/hardware/URDF/robots/Poppy_Humanoid.URDF#L756) should be positive instead.

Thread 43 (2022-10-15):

Is Poppy still alive?

jiapei100, 2022-10-15:
Hi, I tried to register [Poppy Forum](https://poppy.discourse.group/), but got the following **ERROR** message:

`Sorry, there was an error authorizing your account. Please try again.`

Just wondering where to print this poppy? Any recommendations?

ymollard, 2022-10-15:
Hi,

Can you try again registering on the forum a bit later in case it was a punctual issue? The forum seems running as usual. If it still shows the same message, your IP might have been banned by mistake, send it to me at `dev _at_ poppy-station.org`.

Local fablabs are usually the right place for 3D printing, search the [fablab map](https://www.fablabs.io/labs/map) to find one, but make sure that they have a sintering machine, since FDM printing is less convenient for this kind of parts (but some people did it with FDM anyway). Otherwise you can use a service provider, e.g. in Europe [Axis](https://www.axishello.com/en/), [Sculteo](https://www.sculpteo.com/en/) and many other... Otherwise you can buy a [complete kit including 3D printed parts](https://www.generationrobots.com/en/279-poppy-opensource-robotics-platform) that would be ready to assemble.

I'm closing this, please try again to register to the forum if you still need help about the assembly of the robot.

Closed 2022-10-15.

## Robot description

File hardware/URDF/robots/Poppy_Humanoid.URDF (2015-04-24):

<?xml version="1.0" encoding="utf-8"?>
<robot name="Poppy_Humanoid">
	<link name="pelvis">
		<inertial>
			<origin xyz="-0.000134932459328483 -0.000399086261064929 0.00195556930608449" rpy="0 0 0"></origin>
			<mass value="0.18520035953947"></mass>
			<inertia ixx="0.000101804322229161" ixy="3.56589402562651E-08" ixz="-1.38613151054156E-05" iyy="0.000142404075398435" iyz="-3.50682832702007E-06" izz="9.38193247222871E-05"></inertia>
		</inertial>
		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
		<mass>0.18508</mass>
	</link>
	<link name="r_hip">
		<inertial>
			<origin xyz="-0.0419310610774408 0.0190565121211527 -0.0049369159749795" rpy="0 0 0"></origin>
			<mass value="0.0843835237958419"></mass>
			<inertia ixx="2.80785419197495E-05" ixy="-1.23046307113086E-06" ixz="6.6239556232755E-07" iyy="2.83383567782285E-05" iyz="-1.44609279432087E-06" izz="2.15931686710985E-05"></inertia>
		</inertial>
		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
		<mass>0.08433</mass>
	</link>
	<link name="r_hip_motor">
		<inertial>
			<origin xyz="0.00012677211714017 -0.0228896110294103 -0.0134988950219984" rpy="0 0 0"></origin>
			<mass value="0.0831707898707576"></mass>
			<inertia ixx="2.94087635631147E-05" ixy="-1.19904545841814E-08" ixz="-2.40263672865729E-07" iyy="3.59801748266375E-05" iyz="7.9755837503152E-07" izz="2.29200602273928E-05"></inertia>
		</inertial>
		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
		<mass>0.13848</mass>
	</link>
	<link name="r_thigh">
		<inertial>
			<origin xyz="0.0192501209789311 -0.140974172218775 0.000432765258959229" rpy="0 0 0"></origin>
			<mass value="0.116386255838466"></mass>
			<inertia ixx="0.000357762131890894" ixy="-4.71321103204108E-05" ixz="2.18885095933642E-06" iyy="5.14619739065129E-05" iyz="-5.54069244270054E-06" izz="0.000370171570432626"></inertia>
		</inertial>
		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
		<mass>0.12066</mass>
	</link>
	<link name="r_shin">
		<inertial>
			<origin xyz="-0.00150809388022299 -0.137041584549603 0.0228988594303728" rpy="0 0 0"></origin>
			<mass value="0.115582219792398"></mass>
			<inertia ixx="0.000397225397723862" ixy="-1.73262609639968E-05" ixz="1.32921239310872E-08" iyy="3.98086710206889E-05" iyz="-5.89721905441721E-07" izz="0.000393657905933943"></inertia>
		</inertial>
		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
		<mass>0.11169</mass>
	</link>
	<link name="r_foot">
		<inertial>
			<origin xyz="0.0204293303781304 -0.0233359048261193 0.0268526073213802" rpy="0 0 0"></origin>
			<mass value="0.0467879950319091"></mass>
			<inertia ixx="8.14403907813341E-05" ixy="1.79180509533517E-07" ixz="-2.42059026946486E-06" iyy="8.8648252995759E-05" iyz="-3.23018791598496E-06" izz="1.79463752431845E-05"></inertia>
		</inertial>
		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
		<mass>0.04674</mass>
	</link>
	<link name="l_hip">
		<inertial>
			<origin xyz="0.0419306472605077 0.0190563885809745 -0.00493699078761145" rpy="0 0 0"></origin>
			<mass value="0.084384314388701"></mass>
			<inertia ixx="2.80793467645287E-05" ixy="1.23086422338588E-06" ixz="-6.62398430684737E-07" iyy="2.83405782814578E-05" iyz="-1.44600299896268E-06" izz="2.15947433435168E-05"></inertia>
		</inertial>
		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
		<mass>0.08434</mass>
	</link>
	<link name="l_hip_motor">
		<inertial>
			<origin xyz="-0.000127079593402107 -0.0228896103855824 -0.0134988950219984" rpy="0 0 0"></origin>
			<mass value="0.0831707898707576"></mass>
			<inertia ixx="2.94087634441972E-05" ixy="1.14532470512781E-08" ixz="2.40221424306256E-07" iyy="3.59801683348766E-05" iyz="7.97560828147263E-07" izz="2.29200536167144E-05"></inertia>
		</inertial>
		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
		<mass>0.13848</mass>
	</link>
	<link name="l_thigh">
		<inertial>
			<origin xyz="-0.019252460356064 -0.142230931721003 0.000612323159069193" rpy="0 0 0"></origin>
			<mass value="0.114854459344049"></mass>
			<inertia ixx="0.000344974307251891" ixy="4.73949176309948E-05" ixz="-2.2011322605997E-06" iyy="5.11655383215627E-05" iyz="-3.3911468808746E-06" izz="0.000357718491831138"></inertia>
		</inertial>
		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
		<mass>0.12152</mass>
	</link>
	<link name="l_shin">
		<inertial>
			<origin xyz="-0.00150809145543363 -0.137041584769234 -0.0229033576380381" rpy="0 0 0"></origin>
			<mass value="0.11558221959692"></mass>
			<inertia ixx="0.000397225344473892" ixy="-1.7326274763791E-05" ixz="-3.52146929156471E-09" iyy="3.98086215785412E-05" iyz="5.50111227416849E-07" izz="0.000393657903677591"></inertia>
		</inertial>
		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
		<mass>0.11169</mass>
	</link>
	<link name="l_foot">
		<inertial>
			<origin xyz="-0.020427799658059 -0.023322293418243 0.0268332758297585" rpy="0 0 0"></origin>
			<mass value="0.0468257348098641"></mass>
			<inertia ixx="8.1463512692765E-05" ixy="-1.79215713282762E-07" ixz="2.42595321155028E-06" iyy="8.8658680494918E-05" iyz="-3.23538234039819E-06" izz="1.7963767676241E-05"></inertia>
		</inertial>
		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
		<mass>0.04678</mass>
	</link>
	<link name="abs_motors">
		<inertial>
			<origin xyz="-6.29779489192246E-05 0.0133591399673186 -0.0195687625589375" rpy="0 0 0"></origin>
			<mass value="0.16766708386429"></mass>
			<inertia ixx="0.000151720676825684" ixy="-2.41666285846992E-07" ixz="-2.06688911297549E-07" iyy="0.000131382009077746" iyz="-2.13904639264389E-06" izz="6.52732386194484E-05"></inertia>
		</inertial>
		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
		<mass>0.27838</mass>
	</link>
	<link name="abdomen">
		<inertial>
			<origin xyz="4.70358640929572E-07 0.0445314260459549 -0.022296044885406" rpy="0 0 0"></origin>
			<mass value="0.0384110457457536"></mass>
			<inertia ixx="5.9365236572053E-05" ixy="-8.257716306361E-11" ixz="-2.55036869156096E-10" iyy="5.98640694082658E-05" iyz="3.94818292640265E-07" izz="2.35987614893539E-05"></inertia>
		</inertial>
		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
		<mass>0.03839</mass>
	</link>
	<link name="spine">
		<inertial>
			<origin xyz="-2.40411891850495E-07 0.0288451667347867 -0.0100975118547382" rpy="0 0 0"></origin>
			<mass value="0.0926815106655512"></mass>
			<inertia ixx="3.84763910015325E-05" ixy="-1.20593001730888E-09" ixz="-2.38589260905183E-10" iyy="2.7320514654861E-05" iyz="1.47490149318973E-06" izz="3.26595211965373E-05"></inertia>
		</inertial>
		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
		<mass>0.09264</mass>
	</link>
	<link name="bust_motors">
		<inertial>
			<origin xyz="3.50872416629779E-05 0.0105220286877652 -0.0174331453843439" rpy="0 0 0"></origin>
			<mass value="0.158876054570625"></mass>
			<inertia ixx="0.000100953683249293" ixy="-3.89105307189684E-07" ixz="9.71749941401585E-08" iyy="8.94288410563621E-05" iyz="-1.31738255727689E-06" izz="4.26225972692235E-05"></inertia>
		</inertial>
		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
		<mass>0.15889</mass>
	</link>
	<link name="chest">
		<inertial>
			<origin xyz="2.35256459143538E-06 0.0514948183080913 -0.0105463056982622" rpy="0 0 0"></origin>
			<mass value="0.262925523172723"></mass>
			<inertia ixx="0.000154597294293882" ixy="2.32304239504647E-08" ixz="-2.47140128362103E-08" iyy="0.000750952782458072" iyz="1.53530143139102E-06" izz="0.000688549998744818"></inertia>
		</inertial>
		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
		<mass>0.27528</mass>
	</link>
	<link name="neck">
		<inertial>
			<origin xyz="-0.00147486363077957 0.00928455262636602 2.89600749219313E-06" rpy="0 0 0"></origin>
			<mass value="0.00588496516988365"></mass>
			<inertia ixx="7.25596636570396E-07" ixy="-9.29944216419538E-08" ixz="2.01438227027406E-10" iyy="2.33535976458607E-06" iyz="1.55383710797264E-11" izz="2.57395421284165E-06"></inertia>
		</inertial>
		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
		<mass>0.00588</mass>
	</link>
	<link name="head">
		<inertial>
			<origin xyz="0.000557544173188459 0.0327437693305889 -0.0132545775103434" rpy="0 0 0"></origin>
			<mass value="0.188564323997503"></mass>
			<inertia ixx="0.000353329921483274" ixy="-2.17595216032547E-07" ixz="4.10678991843685E-06" iyy="0.000384587155295662" iyz="-2.16656424152966E-05" izz="0.000396626339401006"></inertia>
		</inertial>
		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
		<mass>0.2126</mass>
	</link>
	<link name="l_shoulder">
		<inertial>
			<origin xyz="0.0105246491971973 0.00179805316216127 -0.00915201992957032" rpy="0 0 0"></origin>
			<mass value="0.00843598968780806"></mass>
			<inertia ixx="3.39606863056539E-06" ixy="-4.79545875245114E-08" ixz="2.95435354929514E-08" iyy="3.56726082486902E-06" iyz="1.00382310579659E-08" izz="1.84634806401887E-06"></inertia>
		</inertial>
		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
		<mass>0.00838</mass>
	</link>
	<link name="l_shoulder_motor">
		<inertial>
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

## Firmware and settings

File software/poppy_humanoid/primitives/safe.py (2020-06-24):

import platform
import logging
import subprocess

import pypot.primitive

logger = logging.getLogger(__name__)

class LimitTorque(pypot.primitive.LoopPrimitive):
    def __init__(self, robot, freq=20, max_error=10., torque_min=20., torque_max=95.):
        pypot.primitive.LoopPrimitive.__init__(self, robot, freq)

        self._max_error = max_error
        self.torque_min = torque_min
        self.torque_max = torque_max

    def setup(self):
        self.initial_torque_limit = []

        # Using a dictionnary may be a better solution so we can easily retrieve the initial torque value.
        for m in self.robot.motors:
            self.initial_torque_limit.append(m.torque_limit)

        self.active_motors = self.robot.motors

    def update(self):
        for m in self.active_motors:
            self.adjust_torque(m)

    def adjust_torque(self, motor):
        target = motor.goal_position
        pos = motor.present_position
        dist = abs(target - pos)

        if dist > self._max_error:
            motor.torque_limit = self.torque_max
        else:
            motor.torque_limit = self.torque_min + dist / self._max_error * (self.torque_max - self.torque_min)

    def teardown(self):
        for m, i in enumerate(self.robot.motors):
            m.torque_limit = self.initial_torque_limit[i]

    @property
    def change_watched_motors(self):
        return self.active_motors

    @change_watched_motors.setter
    def change_watched_motors(self, watched_motors):
        self.active_motors = list(map(self.get_mockup_motor, watched_motors))

    @property
    def max_error(self):
        return self._max_error

    @max_error.setter
    def max_error(self, new_error):
        if new_error <= 0:
            raise ValueError('The max_error parameter must be strictly positive!')
        self._max_error = float(new_error)

    # TODO
    @property
    def add_watched_motors(self):
        raise NotImplementedError('TODO :)')

    @add_watched_motors.setter
    def add_watched_motors(self, added_motors):
        raise NotImplementedError('TODO :)')

    @property
    def remove_watched_motors(self):
        raise NotImplementedError('TODO :)')

    @remove_watched_motors.setter
    def remove_watched_motors(self, suppressed_motors):
        raise NotImplementedError('TODO :)')


class TemperatureMonitor(pypot.primitive.LoopPrimitive):
    '''
        This primitive raises an alert by playing a sound when the temperature
        of one motor reaches the "temp_limit".
        
        On GNU/Linux you can use "aplay" for player
        On MacOS "Darwin" you can use "afplay" for player
        On windows vista+, you can maybe use "start wmplayer"
        '''
    def __init__(self, robot, freq=0.5, temp_limit=55, player=None, sound=None):
        pypot.primitive.LoopPrimitive.__init__(self, robot, freq)

        self.temp_limit = temp_limit
        self.sound = sound
        self.watched_motors = self.robot.legs + self.robot.torso + self.robot.arms
        
        if player is not None:
            self.player = player
        elif 'Windows' in platform.system():
            self.player = 'wmplayer'
        elif 'Darwin' in platform.system():
            self.player = 'afplay'
        else:
            self.player = 'aplay'

    def setup(self):
        pass

    def update(self):
        self.check_temperature()

    def teardown(self):
        pass

    def check_temperature(self):
        motor_list = []

        for m in self.watched_motors:
            if m.present_temperature > self.temp_limit:
                motor_list.append(m)

        if len(motor_list) > 0:
            self.raise_problem(motor_list)

    def raise_problem(self, motor_list):
        try:
            subprocess.call([self.player, self.sound])
        except OSError:
            logger.warning('Sound player {} cannot be started'.format(self.player))

        for m in motor_list:
            print('{} overheating: {}'.format(m.name, m.present_temperature))

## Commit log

2015-01-13 add Poppy Humanoid complete assembly with URDF properties
2015-01-13 add Poppy Humanoid complete assembly with URDF properties
    update assembly
2015-01-14 set geometrical references by hand to avoid error during the export to URDF file
2015-01-30 add LimitTorque loop primitive to reduce the torque applied by motors when idle. add this primitive to the setup of PoppyHumanoid robot.
2015-01-30 change default primitive manager filter to sum()
2015-01-30 add from __future__ import division to avoid problem with python2 int/float division
    [safe.py]
2015-01-30 First URDF config
    [Poppy_Humanoid.URDF]
2015-01-30 update joint axis orientation
    [Poppy_Humanoid.URDF]
2015-01-30 add URDF manifest
2015-01-30 add 3D models (STL files) for the URDF model
    [abdomen.STL, abs_motors.STL, bust_motors.STL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]
2015-01-30 update urdf path to 3D models
    [Poppy_Humanoid.URDF]
2015-01-30 add python script to modify the URDF file following the json configuration of Poppy Humanoid
2015-01-30 URDF file updated
    [Poppy_Humanoid.URDF]
2015-01-30 Add the child script that should be attach to an empty object in any scene intended to work with pypot.
2015-01-30 set back default dynamixel velocity/torque parameters when the dance primitive is stopped
2015-01-30 attach more primitives during the Poppy Humanoid setup
2015-02-05 Add a first version for the Poppy Humanoid BOM
2015-02-16 update documentation for the legs assembly
2015-02-16 add documentation for the Poppy Humanoid assembly
2015-02-18 Add python script and tutorial (!) to extract STL files of 3D printed parts from the Solidworks model.
2015-02-19 update all module documentation to include instructions about the Robotis Dynamixel assembly
2015-02-21 add link to the BOM in each module.
2015-02-24 get current torque limit at the setup and retrieve it at the teardown
2015-02-24 bug forget to replace a poppy_humanoid by a robot in the init
    [safe.py]
2015-02-24 add method to make it possible to change on which motors the primitive should run
2015-03-02 Add export of STL files for the head assembly. Fix #5
    Bonus: Get ride of the *$%!! windows "^M" character
2015-03-18 Update README.md
    add information about where we can find STL files
2015-03-18 Create a simplify convex hull shape around a bunch of meshes
    Work for the CFC: https://forum.poppy-project.org/t/cfc-reduce-3d-meshes-complexity-of-the-urdf-model/1031
    [abs_motors_respondable.stl, bust_motors_respondable.stl, head_respondable.stl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]
2015-03-20 update BOM
2015-03-20 update Poppy Humanoid assembly for 1.0 release
2015-03-25 update head module with tutorial for the wire soldering
2015-03-26 new respondable shape
    [Poppy_Humanoid_collision.URDF, abdomen_respondable.STL, chest_respondable.STL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]
2015-03-27 rebuild of every shapes and modify URDF file
    [Poppy_Humanoid.URDF, abs_motors_respondable.stl, bust_motors_respondable.stl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]
2015-03-27 remove of URDF test file
    [Poppy_Humanoid_collision.URDF]
2015-03-27 rename upper_arm in l_upper_arm
    [upper_arm.STL]
2015-03-27 visual simplified shape
    [Poppy_Humanoid.URDF, abdomen_visual.STL, abs_motors_visual.STL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]
2015-04-01 fix bug in the camera support
2015-04-07 update knee motor configuration for the sitting position
2015-04-07 update angle limit configuration for the Poppy Humanoid's legs
2015-04-07 enable the safe compliance only on the torso motors
2015-04-07 fix wrong motor angle limit orientation for hip_z motors
2015-04-09 update materials properties
2015-04-09 add a new Loop Primitive to monitor the motor temperature
2015-04-09 fix sound playing error
    [safe.py]
2015-04-10 Use new print for python3 compatibility.
2015-04-13 assembly guide, complete but the head
2015-04-21 added some istructions for head assembly
2015-04-23 Odroid part in assembly doc
2015-04-24 modification on concave shape to avoid interaction in V-REP
    [abdomen_respondable.STL, chest_respondable.STL]
2015-04-24 update link masses add masses in the update_URDF scripts.
    [Poppy_Humanoid.URDF]
2015-04-24 changing script force for tunning in pypot (+6 squashed commits) Squashed commits: [34310c2] new V-REP optimized scene for Bullet engine [ad5473c] ajout timer.lua [00827dc] new scene with a random fo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
    new V-REP optimized scene for Bullet engine
    changing script force for tunning in pypot
2015-04-24 update URDF robot angle limits
    [Poppy_Humanoid.URDF]
2015-04-24 remove head motor group from the motor list of temperature monitoring. Not sure it is a good idea ...
2015-05-05 head assembly in assembly doc
2015-06-10 rename assemblyGuide into md file to keep commit tracking
2015-06-10 split the assembly guide into smaller markdown file so it can be modularized.
2015-07-01 checked and mini modifs on en assembly doc
2015-07-02 assemblage bras
2015-07-02 assemblage tronc
2015-07-02 assemblage jambes
2015-07-03 assemblage tete + deplacement images
2015-07-06 integrated final assembly videos if sub parts poppy_humanoid_assembly_instruction only contains links
2016-01-15 remove temperature-monitoring primitive from vrep
2016-05-25 fix OSError in V-REP
    [safe.py]
2016-05-31 Update README.md
    Fix reference to the assembly documentation
2020-10-28 modify robot intsanciation with/without camera
2020-10-28 Add bloc "sensors": { "camera...
    To allow a start API from puppet with the camera activated if any....
2021-12-06 Drop the old version of the BOM

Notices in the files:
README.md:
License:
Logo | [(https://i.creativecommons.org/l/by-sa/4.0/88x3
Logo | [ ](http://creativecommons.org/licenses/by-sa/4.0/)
